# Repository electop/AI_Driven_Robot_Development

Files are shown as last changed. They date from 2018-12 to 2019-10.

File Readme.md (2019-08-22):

# Robot artist on the Champs Elysees
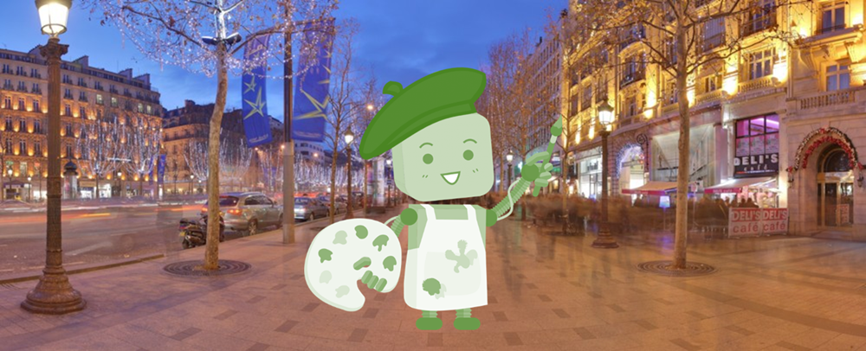
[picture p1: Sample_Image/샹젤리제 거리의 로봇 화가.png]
<br>

# Candidates for AI Driven Robot Development
1. Drawing Robot - Arduino Uno + CNC Shield + GRBL (May 27, 2017)<br>
https://www.thingiverse.com/thing:2349232<br>
https://www.youtube.com/watch?time_continue=3&v=vTD7USqdXJI<br>
Drawing Robot - Arduino Uno + CNC Shield + GRBL<br>
2. EEZYxyDRAW (Aug 24, 2018)<br>
https://www.thingiverse.com/thing:2936872<br>
EEZYxyDRAW<br>
3. drawbot (Sep 12, 2018)<br>
https://www.thingiverse.com/thing:3096135<br>
drawbot<br>
4. Cosmos Drawbot 1.0 (May 12, 2019)<br>
https://www.thingiverse.com/thing:3624736<br>
Cosmos Drawbot 1.0<br>
5. midTbot (Oct 16, 2017)<br>
https://www.thingiverse.com/thing:2587684<br>
http://www.buildlog.net/blog/2017/10/the-midtbot-a-new-flavor-of-h-bot/<br>
midTbot<br>
    - PCB DipTrace file : <a href="http://www.buildlog.net/blog/wp-content/uploads/2017/10/MidTBot_PCB_V1.zip">MidTBot_PCB_V1</a><br>
    - PCB Gerber file : <a href="http://www.buildlog.net/blog/wp-content/uploads/2017/10/midTbot_Gerber_v1.zip">midTbot_Gerber_v1</a>

# Summary for Drawing Robot
   - Configuration
        ```
        $0=10 (step pulse, usec)
        $1=25 (step idle delay, msec)
        $2=0 (step port invert mask:00000000)
        $3=0 (dir port invert mask:00000000)
        $4=0 (step enable invert, bool)
        $5=0 (limit pins invert, bool)
        $6=0 (probe pin invert, bool)
        $10=3 (status report mask:00000011)
        $11=0.010 (junction deviation, mm)
        $12=0.002 (arc tolerance, mm)
        $13=0 (report inches, bool)
        $20=0 (soft limits, bool)
        $21=0 (hard limits, bool)
        $22=0 (homing cycle, bool)
        $23=0 (homing dir invert mask:00000000)
        $24=25.000 (homing feed, mm/min)
        $25=500.000 (homing seek, mm/min)
        $26=250 (homing debounce, msec)
        $27=1.000 (homing pull-off, mm)
        $100=100.000 (x, step/mm) > GT2 Pully : 내경 5mm, 외경 13mm, 높이 14mm, Pitch 2mm, 16 teeth
        $101=100.000 (y, step/mm)
        $102=100.000 (z, step/mm)
        $110=3000.000 (x max rate, mm/min)
        $111=3000.000 (y max rate, mm/min)
        $112=3000.000 (z max rate, mm/min)
        $120=1000.000 (x accel, mm/sec^2)
        $121=1000.000 (y accel, mm/sec^2)
        $122=1000.000 (z accel, mm/sec^2)
        $130=300.000 (x max travel, mm)
        $131=220.000 (y max travel, mm)
        $132=200.000 (z max travel, mm)
        ```
   - Contents<br>
      This drawing robot is similar to the commercially available AxiDraw. It is powered by an Arduino Uno controller, uses a CNC Shield, and GRBL firmware. The approximate cost to build this drawing robot is $100.

      Assembly documentation can be found in the Files section and at the following link. Thanks to Jonathan K for supplying this documentation.<br>
      https://docs.google.com/presentation/d/1GihJuR7yHVtUPYCp9GVDHLsJUhT2RwPrkIopzYrXYhw/edit?usp=sharing

      There's also a document which explains how to install Inkscape, the Inkscape MI extension, and the Universal G-Code Sender. It guides you through three example projects and can be found in the Files section of this Thing. Use these instructions instead of the last three pages of the assembly document which describe a different G-Code extension.

      This drawing robot allows you to draw things in Inkscape and then plot them out. The drawing robot receives G Code commands that are created inside an Inkscape extension called MI. Below are the links to the software used. There's a document in the Files section explaining how to use the software.

      Print all the parts. Assemble them using the assembly guide and then use the installation and use guide to start using your Draw Robot.

      When setting up your hardware you must do the following:

      1. Be sure to install 3 jumpers on the CNC Shield for each stepper driver. There's a photo showing the jumpers.
      2. You must use the GRBL version pointed to in the link below. Replace the "config.h" file with the one provided which has the correct features enabled before you compile and download from the Arduino IDE. IF YOU FAIL TO PERFORM THIS STEP, the robot will draw at a 45 degree angle. Don't send me a message about this because it means you failed to perform this step
      3. Set the GRBL parameters to the settings that are provided in one of the photos. This step is missing from the otherwise excellent instructions. You must do this or the robot will not work.
      4. Be sure to set the correct MI Extension parameters the first time you get the MI extension pop up.
      5. If you have problems with your stepper motors moving and you believe everything else above is OK, check that the small current adjustment on your stepper drivers are set mid point and also set the drive current to 1 amp using the correct procedure for your driver.

      I have posted all the parts needed from the two source designs. There are only 15 parts to print and none of them are very large. I added a stronger pen slider and a controller enclosure. There is an even better pen holder in the remix section. I also clarified the names that were in Spanish. I have posted all needed files so that there isn't confusion regarding which parts are needed from each of the original designs.

      My drawing robot is modified version of this one<br>
      https://www.thingiverse.com/thing:2058866

      Place this version of GRBL Firmware for the Arduino on your computer. You must use this version of GRBL. Other GRBL versions do not have the control code for the Z axis servo.<br>
      https://github.com/robottini/grbl-servo

      Replace the default config.h file in GRBL with the one supplied in the "Thing Files" section

      Upload GRBL to your Arduino Uno using these instructions<br>
      https://github.com/grbl/grbl/wiki/Compiling-Grbl (Ignore references to GRBL V1.1)<br>
      You must copy the config.h which I supply here to the directory where GRBL resides and then do the upload. The new config.h will be used for the compile of the GRBL code.

      Inkscape Drawing Software<br>
      https://inkscape.org/en/

      Universal G-Code Sender<br>
      https://winder.github.io/ugs_website/download/<br>

      Use the Inkscape MI Extension to generate G Code:<br>
      http://www.mediafire.com/file/ae0wquqornzc3o2/MI+Inkscape+Extension.zip<br>
      There is a tutorial in the Files section on how to use the software.

## HARDWARE NEEDED<br>
2x Nema 17 Stepper Motors<br>
2x Linear bearing rod M8 x 450mm, X Axis<br>
2x Linear bearing rod M8 x 350mm, Y axis<br>
2x Linear rod M3 x 75mm, Z Axis<br>
(You can find them in any old CDROM or purchase on EBay)<br>
1x M8x470mm threaded rod<br>
8x LM8UU linear bearings or printed bearings<br>
1x sg90 Servo<br>
2x GT2 Pulley 16 teeth<br>
5x Bearing 624zz<br>
1x 2000mm GT2 belt

misc M3 and M4 screws and nuts<br>
M8 nuts

## ELECTRONICS<br>
Arduino Uno<br>
CNC Shield<br>
12V 2A Wall Transformer<br>
https://www.amazon.com/Adapter-100-240V-Transformers-Switching-Adaptor/dp/B019Q3U72M<br>
2-4 limit switches ( optional. I suggest you leave them off and add later if you want them)

## SOFTWARE<br>
Inkscape which is the graphics design software (draw or import graphics)<br>
Inkscape MI GRBL Extension (convert graphics to G-Code)<br>
Universal G Code Sender (sends the G-Code to the robot causing drawing motion)<br>
GRBL which is the Arduino firmware (programmed into the Arduino Uno)

I have supplied a few G Code files that work with this drawing robot. If your drawing robot is built identical to this design, the G Code files will also work with yours.

Here are a couple of videos of this drawing robot in action:<br>
https://youtu.be/vTD7USqdXJI<br>
https://youtu.be/kpTIFBDcTaY

Update 6-15-2017: I added the limit switches about 10 days ago and they don't add much to the functionality. When GRBL sees a limit switch hit, it just stops with an alarm condition. You must soft reset the robot and your drawing cannot be continued. The homing feature doesn't seem to work. I read in another persons post that they could not get home to work in GRBL 0.9. At this point I suggest building the drawing robot without the limit switches. As long as your drawing does not exceed the envelope of the robot, you won't need the limit switches.

Update 6-19-2017: My friend found a better Inkscape Extension for generating G Code.<br>
I think the MI Extension is easier to use and generates better G Code:<br>
http://www.mediafire.com/file/ae0wquqornzc3o2/MI+Inkscape+Extension.zip

Update 6-26-2017:<br>
I added the config.h file needed for GRBL for this machine. With this file and the GRBL parameter settings in the screen shot, you should be able to easily get your machine up and running. Don't forget to install the stepper driver jumpers.

Update 7-4-2017:<br>
The top and bottom clam shells did not fit without pushing the LM8UU bearings slightly out of alignment. I removed a small amount of material from the top clamshell to allow clearance for the bottom clamshell posts. The old Top_XY_clamshell.stl file has been removed and replaced with the Top_XY_clamshell_V4.stl file. Thanks to rocketmannate who caught this problem.

Update 11-18-2017<br>
Jonathan K. provided assembly documentation. Thanks you so much. I appreciate your efforts. Checkout the great PDF with excellent photos.

Update 3-11-2018<br>
I have had some questions from people whose drawing robots didn't work. Here are some things to check If your robot doesn't work:
Here are some things to check If your robot doesn't work:
Make sure you have the correct version of GRBL (the one pointed to in the description)
Make sure you copied the config.h file to your GRBL directory
Check your CNC jumpers. All three should be installed
Check that you entered the GRBL parameters using Universal G-Code sender
If your Z axis motor isn't working, make sure you have the correct version of GRBL and that you wired your servo to the correct pins.
Make sure you used the MI extension parameters shown in screenshot specifically M3 and M5 for up and down on Z servo

Update: Sept. 18, 2018<br>
If you have problems with your stepper motors moving and you believe everything else above is OK, check that the small current adjustment on your driver is set mid point and then set the drive current to 1 amp using the correct procedure for your driver.
Thanks to Ashkangh for catching this possible issue.

Update: January 4, 2019<br>
A few people have run into software errors when using the GRBL MI Extension. This extension depends on a software package called Python. Your computer may not have this package or it may have one that is older or newer than the one this robot was tested with. I suggest that you do a Google search if you get a xxxx.py" error and follow the instructions for correcting code or installation of Python.

Also:<br>
There are various Stepper Motor drivers that are slightly different. in some cases the current adjust pot is on the opposite end of the module which can be confusing when trying to plug it in based on my photos. Be sure to check the pin names and plug your module in with the pin names that match. I'm sorry but I don't have time to figure out your individual hardware configuration problems. This design works but it can require some troubleshooting if software or hardware is different than what I happened to use. When you figure out your problem, be sure to post the solution in the comments so that others may benefit from your experience.

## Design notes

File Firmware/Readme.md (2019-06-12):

### How to export hex file from arduino uno, using IDE
   - cmd
   - cd C:\Program Files (x86)\Arduino\hardware\tools\avr\bin
   - if com port is com7, execute "avrdude.exe -p m328p  -c arduino -C "..\etc\avrdude.conf" -P com7 -U flash:r:"C:\flash.hex":i" on "명령 프롬프트"
   ```
   C:\Program Files (x86)\Arduino\hardware\tools\avr\bin>avrdude.exe -p m328p  -c arduino -C "..\etc\avrdude.conf" -P com7 -U flash:r:"C:\flash.hex":i

   avrdude.exe: AVR device initialized and ready to accept instructions

   Reading | ################################################## | 100% 0.00s

   avrdude.exe: Device signature = 0x1e950f (probably m328p)
   avrdude.exe: reading flash memory:

   Reading | ################################################## | 100% 4.10s

   avrdude.exe: writing output file "C:\flash.hex"

   avrdude.exe: safemode: Fuses OK (E:00, H:00, L:00)

   avrdude.exe done.  Thank you.
   ```

### How to flash hex file into arduino uno, using IDE
   - cmd
   - cd C:\Program Files (x86)\Arduino\hardware\tools\avr\bin
   - if com port is com7 and there is hex file at C drive root, execute "avrdude.exe -p m328p  -c arduino -C "..\etc\avrdude.conf" -P com7 -U flash:w:"C:\flash.hex":i" on "명령 프롬프트"<br>
     if there is no available hex file, please use 'falsh.hex' on this path.
   ```
   C:\Program Files (x86)\Arduino\hardware\tools\avr\bin>avrdude.exe -p m328p  -c arduino -C "..\etc\avrdude.conf" -P com7 -U flash:w:"C:\flash.hex":i

   avrdude.exe: AVR device initialized and ready to accept instructions

   Reading | ################################################## | 100% 0.00s

   avrdude.exe: Device signature = 0x1e950f (probably m328p)
   avrdude.exe: NOTE: "flash" memory has been specified, an erase cycle will be performed
                To disable this feature, specify the -D option.
   avrdude.exe: erasing chip
   avrdude.exe: reading input file "C:\flash.hex"
   avrdude.exe: writing flash (32768 bytes):

   Writing | ################################################## | 100% 5.39s

   avrdude.exe: 32768 bytes of flash written
   avrdude.exe: verifying flash memory against C:\flash.hex:
   avrdude.exe: load data flash data from input file C:\flash.hex:
   avrdude.exe: input file C:\flash.hex contains 32768 bytes
   avrdude.exe: reading on-chip flash data:

   Reading | ################################################## | 100% 4.13s

   avrdude.exe: verifying ...
   avrdude.exe: 32768 bytes of flash verified

   avrdude.exe: safemode: Fuses OK (E:00, H:00, L:00)

   avrdude.exe done.  Thank you.
   ```

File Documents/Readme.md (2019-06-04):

# CR-10S & 10S4 & 10S5 사용정보(20190522)

## CR-10S & 10S4 & 10S5
출력방식 : FDM(Fused DEposition Modeling)<br>
출력사이즈 : 300*300*400 / 400*400*400 / 500*500*500<br>
프린터크기 : 525*270*635 / 610*290*740 / 730*285*840<br>
프린팅속도 : Normal 80mm/s, Max 200mm/s<br>
필라멘트 사이즈 : 1.75mm<br>
레이어두께 : 0.1~0.4mm (권장)<br>
노즐직경 : 0.4mm (0.2~1mm 사용가능, 0.4mm 사용추천)<br>
정밀도 : +(-)0.1mm<br>
익스트루더 : MK8 방식<br>
지원파일포맷 : STL, OBJ, G-Code<br>
입력방식 : USB(OnLine), SD Card(OffLine)<br>
무게 : 10.3kg / 11.5kg / 15.6kg<br>
기타사항 :<br>
- CR-10과 차이점 : Z축스텝모터가 더블, 필라멘트 감지센서<br>
- 정전시 이어서 출력가능<br>
- CR-10 시리즈와 엔더3는 레이저 각인기 운용이 가능합니다. https://cafe.naver.com/ddyair/999<br>

## 제품 판매링크
10S : http://dyairkorea.com/product/detail.html?product_no=12&cate_no=47&display_group=1<br>
10S4 : http://dyairkorea.com/prouct/detail.html?product_no=86&cate_no=47&display_group=1<br>
10S5 : http://dyairkorea.com/product/detail.html?product_no=25&cate_no=47&display_group=1<br>

**스페어파트**<br>
프로파일롤러 http://dyairkorea.com/product/detail.html?product_no=59&cate_no=31&display_group=1<br>
팬세트 http://dyairkorea.com/product/detail.html?product_no=56&cate_no=31&display_group=1<br>
스텝모터 http://dyairkorea.com/product/detail.html?product_no=51&cate_no=31&display_group=1<br>
http://dyairkorea.com/product/detail.html?product_no=50&cate_no=31&display_group=1<br>
커플러 http://dyairkorea.com/product/detail.html?product_no=47&cate_no=31&display_group=1<br>
빌드서페이스 http://dyairkorea.com/product/detail.html?product_no=58&cate_no=31&display_group=1<br>
파워서플라이 http://dyairkorea.com/product/detail.html?product_no=49&cate_no=31&display_group=1<br>
메인보드 http://dyairkorea.com/product/detail.html?product_no=48&cate_no=31&display_group=1<br>
히팅베드 http://dyairkorea.com/product/detail.html?product_no=53&cate_no=31&display_group=1<br>
LCD디스플레이 http://dyairkorea.com/product/detail.html?product_no=52&cate_no=31&display_group=1<br>
MK8 익스트루더 http://dyairkorea.com/product/detail.html?product_no=64&cate_no=31&display_group=1<br>
Z축지지대 http://dyairkorea.com/product/detail.html?product_no=61&cate_no=31&display_group=1<br>

## 기본적으로 알아야 할 내용

- 조립 : https://cafe.naver.com/ddyair/82<br>
- 베드레벨링 : https://cafe.naver.com/ddyair/85<br>
- 큐라설치 및 세팅 : 10S https://cafe.naver.com/ddyair/4865<br>
  10S5 https://cafe.naver.com/ddyair/4866<br>
- 노즐교체 영상(CR시리즈과 동일) : https://www.youtube.com/watch?v=Yhu3SahbN44<br>
- 4010팬 교체 동영상입니다.(팬 전압은 12V) : https://www.youtube.com/watch?v=Xu0QXxP7dHU&list=PL5UfhdgCEfhNQBHFDc15D-m7l7TStda3M&index=7&t=0s<br>
  구입처 : https://smartstore.naver.com/ssack3dprinterstore_dyair/products/3046827558<br>
- 노즐세트 교체 방법 : https://www.youtube.com/watch?v=AcJJXZxm2D4&list=PL5UfhdgCEfhNQBHFDc15D-m7l7TStda3M&index=9&t=0s<br>
- 구입처 : https://smartstore.naver.com/ssack3dprinterstore_dyair/products/3045667993<br>
- 조립 후 점검사항 : https://cafe.naver.com/ddyair/84<br>
- 콘트롤박스 메뉴 설명 : https://cafe.naver.com/ddyair/91<br>
- 테스트 리트렉션 : https://cafe.naver.com/ddyair/172<br>
- 출력온도 : https://cafe.naver.com/ddyair/157<br>
- 매쉬레벨링 업데이트 방법 : https://cafe.naver.com/ddyair/1265<br>
  2.0.0 베타버전 : https://cafe.naver.com/ddyair/3384<br>
- 출력물품질 높이는 히트브레이크(모델링 공유 사이트에서 다양한 형태를 선택할수 있습니다.)<br>
  https://cafe.naver.com/ddyair/1410<br>
- 오토레벨링 (Creality3D 센서) : https://cafe.naver.com/ddyair/1538<br>
- BL터치 설치 : https://cafe.naver.com/ddyair/2705<br>
  https://cafe.naver.com/ddyair/2735

## 제품관련 정보

- 출력 품질문제중 가장 많은 포인트, 익스트루더 업그레이드 추천 : https://cafe.naver.com/ddyair/3384<br>
구입처 : https://smartstore.naver.com/ssack3dprinterstore_dyair/products/3707329970<br>
프로파일 T너트 규격 검색 => 2020 T너트<br>
작동시 소모전력 테스트 : https://cafe.naver.com/ddyair/1159

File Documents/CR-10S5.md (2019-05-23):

# CR-10S & 10S4 & 10S5 사용정보(20190522)

## CR-10S & 10S4 & 10S5

출력방식 : FDM(Fused DEposition Modeling)

출력사이즈 : 300*300*400 / 400*400*400 / 500*500*500

프린터크기 : 525*270*635 / 610*290*740 / 730*285*840

프린팅속도 : Normal 80mm/s, Max 200mm/s

필라멘트 사이즈 : 1.75mm

레이어두께 : 0.1~0.4mm (권장) 

노즐직경 : 0.4mm (0.2~1mm 사용가능, 0.4mm 사용추천)

정밀도 : +(-)0.1mm

익스트루더 : MK8 방식

지원파일포맷 : STL, OBJ, G-Code

입력방식 : USB(OnLine), SD Card(OffLine)

무게 : 10.3kg / 11.5kg / 15.6kg

기타사항 :

- CR-10과 차이점 : Z축스텝모터가 더블, 필라멘트 감지센서

- 정전시 이어서 출력가능

- CR-10 시리즈와 엔더3는 레이저 각인기 운용이 가능합니다. https://cafe.naver.com/ddyair/999

## 제품 판매링크
10S : http://dyairkorea.com/product/detail.html?product_no=12&cate_no=47&display_group=1
10S4 : http://dyairkorea.com/prouct/detail.html?product_no=86&cate_no=47&display_group=1
10S5 : http://dyairkorea.com/product/detail.html?product_no=25&cate_no=47&display_group=1

스페어파트
프로파일롤러 http://dyairkorea.com/product/detail.html?product_no=59&cate_no=31&display_group=1
팬세트 http://dyairkorea.com/product/detail.html?product_no=56&cate_no=31&display_group=1
스텝모터 http://dyairkorea.com/product/detail.html?product_no=51&cate_no=31&display_group=1
http://dyairkorea.com/product/detail.html?product_no=50&cate_no=31&display_group=1
커플러 http://dyairkorea.com/product/detail.html?product_no=47&cate_no=31&display_group=1
빌드서페이스 http://dyairkorea.com/product/detail.html?product_no=58&cate_no=31&display_group=1
파워서플라이 http://dyairkorea.com/product/detail.html?product_no=49&cate_no=31&display_group=1
메인보드 http://dyairkorea.com/product/detail.html?product_no=48&cate_no=31&display_group=1
히팅베드 http://dyairkorea.com/product/detail.html?product_no=53&cate_no=31&display_group=1
LCD디스플레이 http://dyairkorea.com/product/detail.html?product_no=52&cate_no=31&display_group=1
MK8 익스트루더 http://dyairkorea.com/product/detail.html?product_no=64&cate_no=31&display_group=1
Z축지지대 http://dyairkorea.com/product/detail.html?product_no=61&cate_no=31&display_group=1

## 기본적으로 알아야 할 내용

- 조립
https://cafe.naver.com/ddyair/82

- 베드레벨링
https://cafe.naver.com/ddyair/85
- 큐라설치 및 세팅
10S https://cafe.naver.com/ddyair/4865
10S5 https://cafe.naver.com/ddyair/4866                                    

- 노즐교체 영상(CR시리즈과 동일)
https://www.youtube.com/watch?v=Yhu3SahbN44

- 4010팬 교체 동영상입니다.(팬 전압은 12V)
https://www.youtube.com/watch?v=Xu0QXxP7dHU&list=PL5UfhdgCEfhNQBHFDc15D-m7l7TStda3M&index=7&t=0s
구입처 https://smartstore.naver.com/ssack3dprinterstore_dyair/products/3046827558

- 노즐세트 교체 방법
 https://www.youtube.com/watch?v=AcJJXZxm2D4&list=PL5UfhdgCEfhNQBHFDc15D-m7l7TStda3M&index=9&t=0s

구입처 https://smartstore.naver.com/ssack3dprinterstore_dyair/products/3045667993

- 조립 후 점검사항
https://cafe.naver.com/ddyair/84                                    

- 콘트롤박스 메뉴 설명
https://cafe.naver.com/ddyair/91

- 테스트
리트렉션 https://cafe.naver.com/ddyair/172   출력온도 https://cafe.naver.com/ddyair/157     

- 매쉬레벨링 업데이트 방법
https://cafe.naver.com/ddyair/1265  2.0.0 베타버전 https://cafe.naver.com/ddyair/3384

- 출력물품질 높이는 히트브레이크(모델링 공유 사이트에서 다양한 형태를 선택할수 있습니다.)  
https://cafe.naver.com/ddyair/1410 

- 오토레벨링 (Creality3D 센서)
https://cafe.naver.com/ddyair/1538

- BL터치 설치
https://cafe.naver.com/ddyair/2705           https://cafe.naver.com/ddyair/2735

## 제품관련 정보

- 출력 품질문제중 가장 많은 포인트, 익스트루더 업그레이드 추천
https://cafe.naver.com/ddyair/3384  
구입처 https://smartstore.naver.com/ssack3dprinterstore_dyair/products/3707329970
프로파일 T너트 규격 검색 => 2020 T너트
작동시 소모전력 테스트 https://cafe.naver.com/ddyair/1159

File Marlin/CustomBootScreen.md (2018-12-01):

Article: http://community.robo3d.com/index.php?threads/custom-boot-screen-for-marlin-and-full-graphics-lcd.17221/
paint.net (image to bmp): https://www.dotpdn.com/files/paint.net.4.1.4.install.zip

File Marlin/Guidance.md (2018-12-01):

https://www.printedsolid.com/blogs/news/installing-marlin-1-1-6-on-your-cr-10s-with-mesh-bed-leveling

<div class="ten columns alpha blog_content">
      <p><strong>Important note about customer support of CR-10S Marlin update blog posts<span>.  These posts were written by David Randolph as a free community contribution.  He's happy to have provided this contribution when Creality would not.  Unfortunately, we do not have unlimited time and cannot provide support if you have any issues with this process.  Please read the instructions carefully and consider your skill level.  If you run into any issues, we suggest posting comments on this blog post as many users </span><span>hang out regularly and will offer help.  Checking into the various Facebook CR-10 Communities is also an option.  </span></strong></p>

<p><strong>UPDATE! </strong>We have added notes for the new version of Marlin 1.1.7 as well as a new download of the source and hex files. Enjoy</p>

<p>Before we start: This is for the <a href="https://printedsolid.com/products/cr10s">CR-10S</a> and not the CR-10. Don’t use this firmware or follow these instructions for the CR-10. It is a different board and uses different settings.The older CR-10 uses a MELZI board which has less memory so in order to get it to work you will have to remove a lot of options to get everything to fit.</p>
<p>The firmware for the CR-10S is based on Marlin <a href="http://marlinfw.org">http://marlinfw.org</a> which is an open source project and as such means you can modify the source code as you want. While this article will be long and involved, I will get right to the point and just give you the .hex file and you can go ahead and just install it and close out this page. This version has mesh bed leveling, baby stepping and EEPROM storage enabled.</p>
<p>Inside the zip is a file called instructions.pdf on how to flash your firmware.</p>
<p> <a href="https://cdn.shopify.com/s/files/1/0887/0138/files/CR-10S-Marlin_By_PrintedSolid.zip?18225442472906648344">CR-10S 1.1.6 Firmware Source Code and Hex Files</a></p>
<p><a href="https://cdn.shopify.com/s/files/1/0887/0138/files/CR-10S-Marlin_By_PrintedSolid_117.zip?18225442472906648344"> CR-10S 1.1.7 Firmware Source Code and Hex Files</a></p>
<p>However, if you’re still reading this then we will go ahead and get moving. Let’s install and configure the software and give you a quick lesson on what we will be doing.</p>
<ol>
<li>You will need to download and install the Arduino IDE. <a href="https://www.arduino.cc/en/Main/Software">https://www.arduino.cc/en/Main/Software</a>
</li>
<li>Next you will need to download and install the U8glib library. <a href="https://bintray.com/olikraus/u8glib/download_file?file_path=u8glib_arduino_v1.18.1.zip">https://bintray.com/olikraus/u8glib/download_file?file_path=u8glib_arduino_v1.18.1.zip</a> and then from inside Arduino go to <em>sketch&gt;include library&gt;add zip library </em>and select the zip file. This is a library used to run the LCD display.</li>
<li>A preference we should setup inside of Arduino is to show line numbers. This will help us guide our way through the code and I will be referring to line numbers and the variable names for version 1.1.6. If you are reading this and using a different firmware version then line numbers may have changed but most likely the variable names will be the same. Now in the Arduino software go to <em>File&gt;Preferences</em> and put a check mark in the box next to Display Line Number.</li>
<li>Finally you need to download the 1.1.6 firmware <a href="http://marlinfw.org/meta/download/">http://marlinfw.org/meta/download/</a> and unzip the folder. Don’t rename the folder or move the files around inside it. You can put it anywhere you like to work on it. Go into the folders till you find Marlin.ino and open that file from inside Arduino IDE. It will open the full project and put all the files into separate tabs along the top.</li>
</ol>
<p>Now we are ready to get to work modifying things. Most of the work we will be doing will be in <em>Configuration.h </em>but we will be touching a few other ones. I will call those out later on. In Arduino if a line is “commented” this means that the instructions on that line are ignored. Marlin is well written and most of what we be doing is uncommenting an option or changing a value of something. To uncomment a line you just remove the two forward slashes // at the beginning of the line. To comment out a line you will just and // at the start of the line.</p>
<h1>Configurations.h</h1>
<p>Line 114: <strong>#define BAUDRATE 115200 </strong></p>
<p><em>This is the speed that it communicates over USB. It could be one of the faster speeds but honestly this is enough.</em></p>
<p>Line 122: <strong>#define MOTHERBOARD BOARD_RAMPS_14_EFB</strong></p>
<p><em>There are many boards that support Marlin and this is one of them. It is based off the very popular board RAMPS.</em></p>
<p>Line 127: <strong>#define CUSTOM_MACHINE_NAME "CR-10S"</strong></p>
<p><em>When your machine starts up this is the name that is displayed in the bottom left of the screen. It can be anything you want between the quotes, even Printer McPrintface if you like.</em></p>
<p>Line 286: (Line 289 in Marlin 1.1.7) <strong>#define TEMP_SENSOR_0 1</strong></p>
<p><em>This sets the type of sensor used for measuring the hotend temperature. For the stock hotend you will use “1” and for an E3Dv6 hotend you will use “5”  </em></p>
<p>Line 291:  (Line 294 in Marlin 1.1.7) <strong>#define TEMP_SENSOR_BED 5</strong></p>
<p><em>This sets the bed sensor for the stock bed.</em></p>
<p>Line 325: (Line 328 in Marlin 1.1.7) <strong>#define HEATER_0_MAXTEMP 250</strong></p>
<p><em>This is the limit for how hot your hotend will go. For the stock hotend you should set it for 250 and for an E3Dv6 hotend you can set it to 300.</em></p>
<p>Line 330: (Line 333 in Marlin 1.1.7) <strong>#define BED_MAXTEMP 120</strong></p>
<p><em>This is the limit for how hot your bed will go. In this case we can set it to 120 but honestly you will be lucky to ever go above 80c.</em></p>
<p>Line 442: (Line 446 in Marlin 1.1.7) <strong>#define THERMAL_PROTECTION_HOTENDS</strong></p>
<p>Line 443: (Line 447 in Marlin 1.1.7)<strong> #define THERMAL_PROTECTION_BED<br></strong></p>
<p><em>These two lines are what protects your machine from thermal runaway. While they are already uncommented I wanted to still point them out so you know to pay attention to them.</em></p>
<p>Line 528: (Line 532 in Marlin 1.1.7) <strong>#define DEFAULT_AXIS_STEPS_PER_UNIT   { 80, 80, 400, 95 }</strong></p>
<p><em>This is the amount of steps your printer has to use to move a specific distance. Things like drivers, motors, gearing, screws can change these numbers but the ones above are good for a stock CR-10S. These can be tuned later from the control screen thanks to the EEPROM settings we will be enabling later.</em></p>
<p>Line 535: (Line 539 in Marlin 1.1.7) <strong>#define DEFAULT_MAX_FEEDRATE          { 2500, 2500, 100, 25 }</strong></p>
<p><em>This is the fastest the machine will move in all directions. </em></p>
<p>Line 553:  (Line 557 in Marlin 1.1.7) <strong>#define DEFAULT_ACCELERATION          575</strong></p>
<p><em></em>Acceleration is the rate of change of speed.  It is defined in mm/s^2.  Your printer slows down when changing direction and then speeds back up again in straight lines.  This line is the acceleration the printer will make during printing moves.  575 is fairly slow, but for a printer like the CR10S with a big moving bed, it will help prevent <a href="https://printedsolid.com/blogs/news/a-solid-foundation-for-high-quality-corners">ringing</a>.  </p>
<p>Line 554: (Line 558 in Marlin 1.1.7) <strong>#define DEFAULT_RETRACT_ACCELERATION  1000</strong></p>
<p><em>This is the acceleration applied to your extruder retraction.  You want this as high as it can go before the filament starts stripping out to help prevent strining.</em></p>
<p>Line 555: (Line 559 in Marlin 1.1.7) <strong>#define DEFAULT_TRAVEL_ACCELERATION   1000</strong></p>
<p><em>This is the acceleration of your printer when it is not printing.  Since it is not printing at the time, it can be a little higher since you won't be able to see the ringing.  If it is too high, you could see skipped steps and layer shifts.</em></p>
<p>Line 745: (Line 751 in Marlin 1.1.7) <strong>#define INVERT_X_DIR false</strong></p>
<p>Line 746: (Line 752 in Marlin 1.1.7) <strong>#define INVERT_Y_DIR false</strong></p>
<p>Line 747: (Line 753 in Marlin 1.1.7) <strong>#define INVERT_Z_DIR true</strong></p>
<p><em>These 3 line define the direction of each axis. If your machine moves in the opposite direction of what you expect then change it to true or false.</em></p>
<p>Line 777: (Line 783 in Marlin 1.1.7) <strong>#define X_BED_SIZE 300</strong></p>
<p>Line 778: (Line 784 in Marlin 1.1.7) <strong>#define Y_BED_SIZE 300</strong></p>
<p>Line 786: (Line 792 in Marlin 1.1.7) <strong> #define Z_MAX_POS 400</strong></p>
<p><em>This is where we set the actual bed size of your printer and the Z height.</em></p>
<p>Line 801: (Line 827 in Marlin 1.1.7) Uncomment <strong>#define FILAMENT_RUNOUT_SENSOR</strong></p>
<p><em>This will enable the filament sensor. </em></p>
<p>Line 803: (Line 829 in Marlin 1.1.7) <strong>#define FIL_RUNOUT_INVERTING true</strong></p>
<p><em>Here we are changing the way the switch on the filament sensor works.</em></p>
<p>Line 855: (Line 876 in Marlin 1.1.7) Uncomment<strong> #define MESH_BED_LEVELING</strong></p>
<p><em>This is the fun part. No probe, no hardware. This allows you to level the bed at multiple points manually and it will create a 3D mesh of the surface to allow you to print on an uneven bed.  It will use the manual bed leveling as defined <a href="http://marlinfw.org/docs/features/unified_bed_leveling.html">here</a>. </em></p>
<p>Line 874:  (Line 986 in Marlin 1.1.7) <strong>#define GRID_MAX_POINTS_X 3</strong></p>
<p><em>We are setting this to 3 which means it will have you level 3 times along the X axis and 3 times along the Y axis for a total of 9 points. If you set this to 5 then it would mean you have to adjust level 25 times on the bed. 3 is a really good number for this.</em></p>
<p>Line 956: (Line 997 in Marlin 1.1.7) Uncomment<strong> #define LCD_BED_LEVELING<br></strong></p>
<p><em>This adds the option to run mesh bed leveling to the LCD screen.</em></p>
<p>Line 964:  (Line 1005 in Marlin 1.1.7) Uncomment<strong> #define LEVEL_BED_CORNERS<br></strong></p>
<p><em>This adds the option to level the corners of your bed before running mesh leveling.</em></p>
<p>Line 1018: (Line 1116 in Marlin 1.1.7) <strong> </strong>Uncomment<strong> #define EEPROM_SETTINGS</strong></p>
<p><em>This allows you to adjust things like offsets and steps and store them.</em></p>
<p>Line 1019: (Line 1117 in Marlin 1.1.7)<strong> </strong>Uncomment<strong> #define DISABLE_M503</strong></p>
<p><em>This is a command that shows the settings as they were set in the firmware and not the ones you changed in the EEPROM. We are disabling this to save some memory.</em></p>
<p>Line 1050 (Line 1148 in Marlin 1.1.7):<strong> #define PREHEAT_1_TEMP_HOTEND 205</strong></p>
<p>Line 1051 (Line 1149 in Marlin 1.1.7):<strong> #define PREHEAT_1_TEMP_BED     60</strong></p>
<p>Line 1052 (Line 1150 in Marlin 1.1.7):<strong> #define PREHEAT_1_FAN_SPEED     0</strong></p>
<p>Line 1054 (Line 1152 in Marlin 1.1.7):<strong> #define PREHEAT_2_TEMP_HOTEND 250</strong></p>
<p>Line 1055 (Line 1153 in Marlin 1.1.7):<strong> #define PREHEAT_2_TEMP_BED     80</strong></p>
<p>Line 1056 (Line 1154 in Marlin 1.1.7):<strong> #define PREHEAT_2_FAN_SPEED     0</strong></p>
<p><em>The lines 1050-1056 set the temps and fan speeds for the menu items to preheat for PLA and ABS.</em></p>
<p>Line 1232: (Line 1330 in Marlin 1.1.7): Uncomment <strong>#define SDSUPPORT</strong></p>
<p><em>This enables the SD card slot so you can print from SD.</em></p>
<p>Line 1257: (Line 1355 in Marlin 1.1.7): Uncomment <strong>#define ENCODER_PULSES_PER_STEP 1</strong></p>
<p><em>Leave this at 1 for the CR-10S</em></p>
<p>Line 1263 (Line 1361 in Marlin 1.1.7): Uncomment <strong>#define ENCODER_STEPS_PER_MENU_ITEM 5</strong></p>
<p><em>This is how far the knob needs to turn to move between menu items. Make this number lower if it is too sensitive and higher if it is not.</em></p>
<p>Line 1303: (Line 1401 in Marlin 1.1.7): Uncomment <strong>#define SPEAKER</strong></p>
<p><em>This will let the machine beep and make sounds.</em></p>
<p>Line 1384 (Line 1482 in Marlin 1.1.7): Uncomment <strong>#define REPRAP_DISCOUNT_FULL_GRAPHIC_SMART_CONTROLLER</strong></p>
<p><em>This enables the LCD screen. When we first installed U8Glib library, it was for this option.</em></p>
<p>Line 1684 (Line 140 in Marlin 1.1.7): #define <strong>DEFAULT_NOMINAL_FILAMENT_DIA 1.75 </strong> </p>
<p><em>Here we set what size filament will be used in the machine.</em></p>

<h1>Configuration_adv.h</h1>
<p>Line 602 (Line 658 in Marlin 1.1.7): Uncomment <strong>#define BABYSTEPPING</strong></p>
<p><em>Baby stepping allows you to adjust the Z axis while printing to help get the perfect 1<sup>st</sup> layer.</em></p>
<p>Line 606 (Line 662 in Marlin 1.1.7):  <strong>#define BABYSTEP_MULTIPLICATOR 5</strong></p>
<p><em>This is how much your Z axis will move per rotation on the knob. I find 5 is a good number but if you want finer control then lower this number. IF you want it to move more per click then increase this number.</em></p>
<p>Line 608 (Line 664 in Marlin 1.1.7): Uncomment <strong>#define DOUBLECLICK_FOR_Z_BABYSTEPPING</strong></p>
<p><em>This makes it so if you want to adjust baby stepping then you can press the control knob two times quickly and you will enter baby step mode.</em></p>
<p>Line 683 (Line 733 in Marlin 1.1.7): Comment out <strong>// #define ARC_SUPPORT</strong></p>
<p><em>Not really used since most slicers don’t do this function by default. If we disable it then we save even more memory.</em></p>
<p>Line 819 (Line 878 in Marlin 1.1.7): Uncomment <strong>#define ADVANCED_PAUSE_FEATURE</strong></p>
<p><em>This is for the filament runout sensor. It will home the hotend and unload the filament from the nozzle. Then once you load more filament it will wait till it’s extruding before beginning the print.</em></p>
<h1>Pins_RAMPS.h</h1>
<p>Line 206 (Line 255 in Marlin 1.1.7): <strong>#define FIL_RUNOUT_PIN      2</strong></p>
<p><em>We are changing this one value from 4 to 2 so we are using the right pin for the filament sensor.</em></p>
<p><em> </em></p>
<h2><strong>All done! Save your work.</strong></h2>
<p>Wow, you really have been sticking with me this whole time and you have modified everything and you are ready to build your firmware and install it. Kudos for sticking with me this whole time.</p>
<ol>
<li>
<em> </em>Select <em>Tools&gt;Board&gt;Arduino/Genuino Mega or Mega 2560</em> and then <em>Tools&gt;Processor&gt;ATMega2560 (Mega 2560) </em>and then select the COM port for your printer. Did I mention that you should have already plugged your printer into your computer?</li>
<li>
<em> </em>Now we want to verify and compile the code. You can do this by clicking on the checkmark icon in the tool bar or by going to <em>Sketch&gt;Verify/Compile </em>
</li>
<li>
<em> </em>If you got no errors then congratulations and now you are ready to upload the firmware. Go to Sketch&gt;Upload or click on the icon in the toolbar that is an arrow pointing to the right.</li>
<li>
<em> </em>Now you are all set and good to go, enjoy your new firmware. Let us know what you think and if you think we should do anything more.</li>
</ol>

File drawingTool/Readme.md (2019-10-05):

## DrawingTool
  ### History
    DrawigTool
    1. v0.001 : 2019-08-23 12:35 by Bongchae Kim
    2. v0.002 : 2019-08-25 11:45 by Bongchae Kim
    3. v0.003 : 2019-09-06 11:34 by Bongchae Kim
    4. v0.004 : 2019-09-09 19:09 by Bongchae Kim
    5. v0.005 : On going

  ### User scenarios
    1. User can import an image file. It's necessary to draw picture as a sketch.
    2. User can get G-codes with a sketch.
    3. User can define the thickness of the line. Of course, it will be also implemented to be able to draw with G-codes, considering the thickness.

  ### Figures
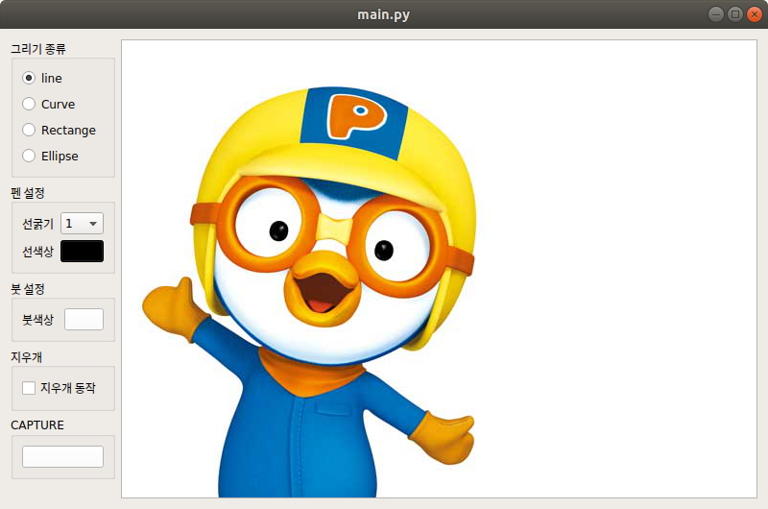
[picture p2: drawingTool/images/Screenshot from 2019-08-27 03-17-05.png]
<br>

## Cartoonizer
  ### History
    1. v0.001 : 2019-08-23 08:31 by Ju-hwan Yoo
    2. v0.002 : On going

  ### User scenarios
    1. User can get cartoon image from web cam device.

  ### Figures
  #### e.g.1
  ##### ▶ Source
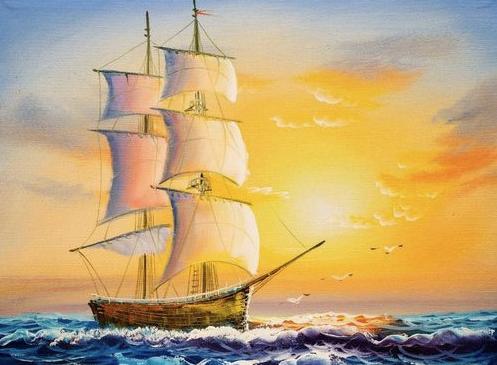
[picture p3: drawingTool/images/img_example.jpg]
  <br>
  ##### ▶ Edge mask
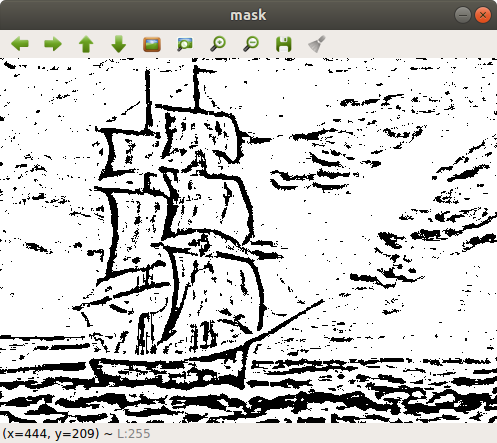
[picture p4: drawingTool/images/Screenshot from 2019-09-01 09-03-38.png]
  <br>
  ##### ▶ Gaussian pyramid + Edge mask
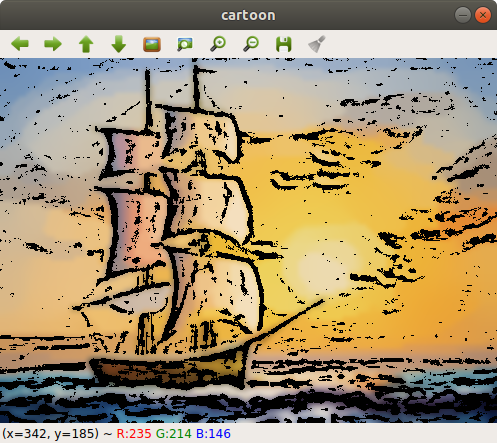
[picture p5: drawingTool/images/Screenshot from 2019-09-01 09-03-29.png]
  <br>
  #### e.g.2
  ##### ▶ Source
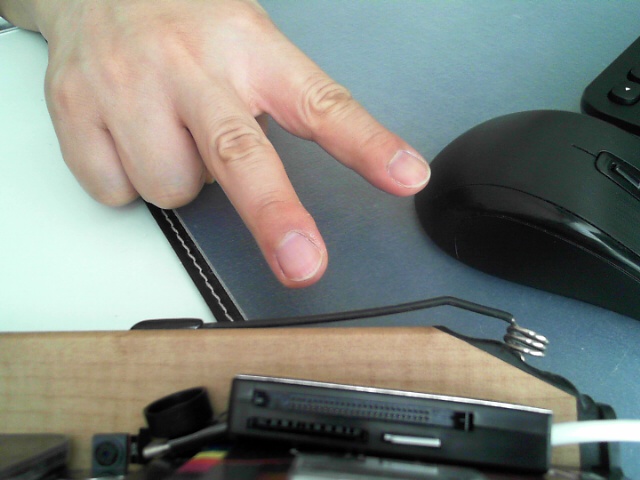
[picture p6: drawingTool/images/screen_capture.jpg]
  <br>
  ##### ▶ Edge mask
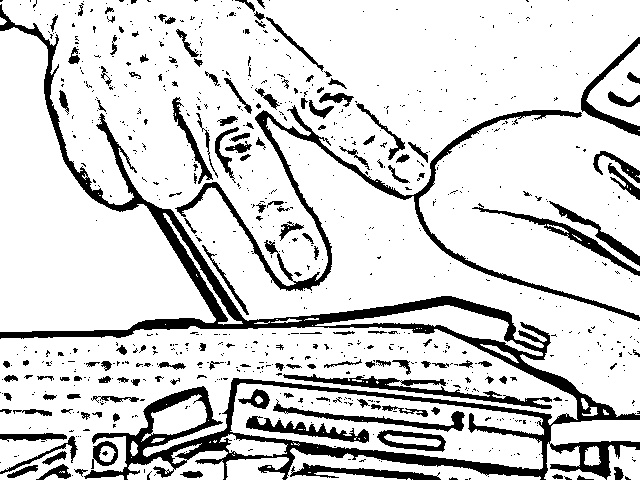
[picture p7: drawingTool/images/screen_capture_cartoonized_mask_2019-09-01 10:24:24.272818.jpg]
  <br>
  ##### ▶ Gaussian pyramid + Edge mask
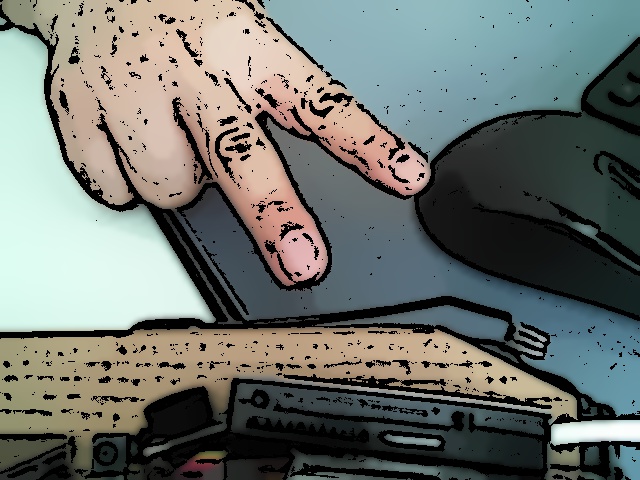
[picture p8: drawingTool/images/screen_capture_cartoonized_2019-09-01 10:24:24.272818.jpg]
  <br>
  #### e.g.3
  ##### ▶ Edge mask (vs) Edge mask + Median blur
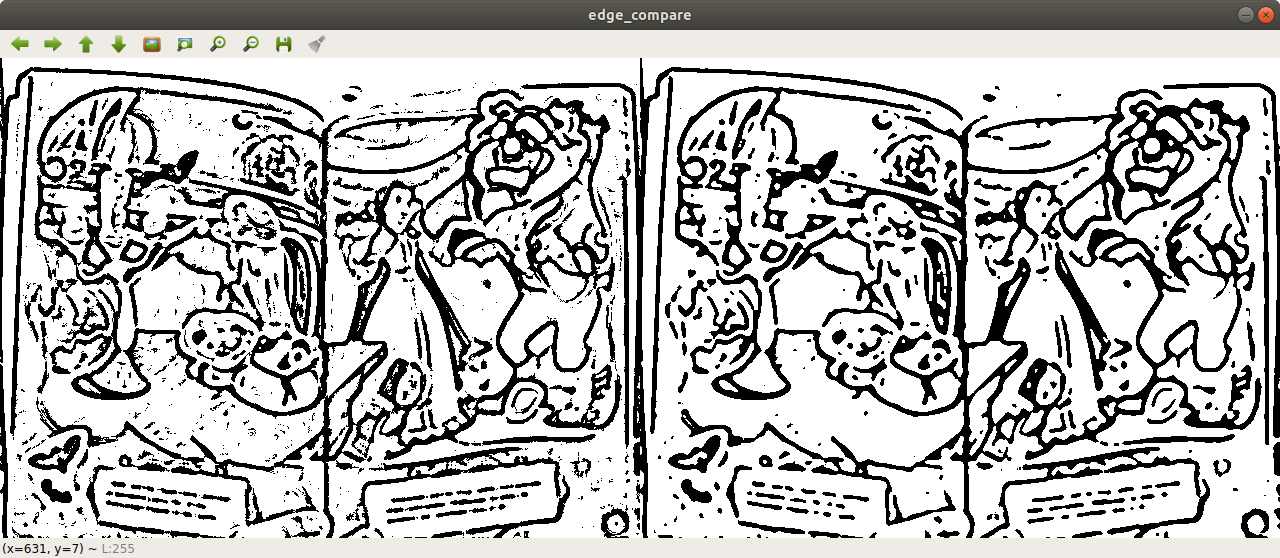
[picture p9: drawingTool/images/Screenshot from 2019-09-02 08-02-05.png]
  <br>
  ##### ▶ Source (vs) Gaussian pyramid + Edge mask + Median blur
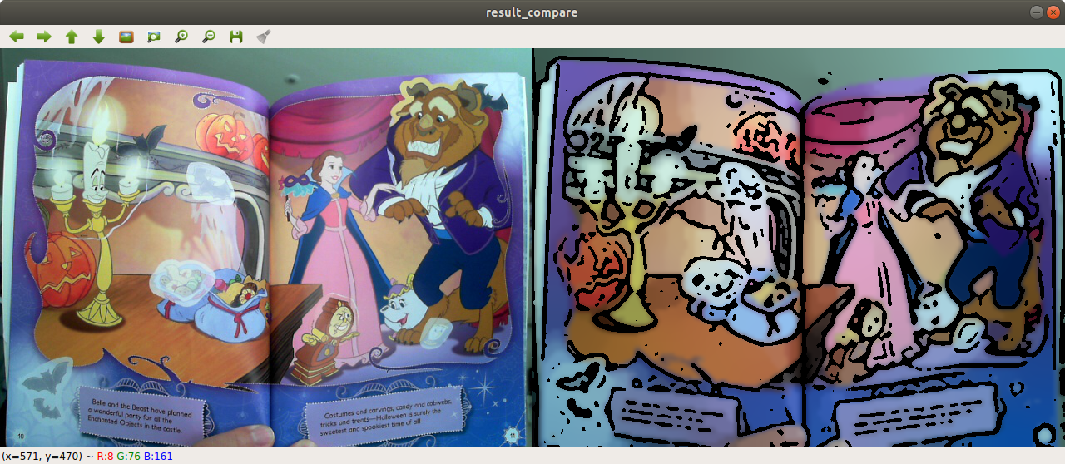
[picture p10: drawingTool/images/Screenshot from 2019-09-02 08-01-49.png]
  <br>

## Drawing Bot Desk design
  ### History
    1. V.0.001 : 2019-09-12 I added laser cutting design for desk.
    
  ### Figures
  #### Design Images
  ##### ▶ Top
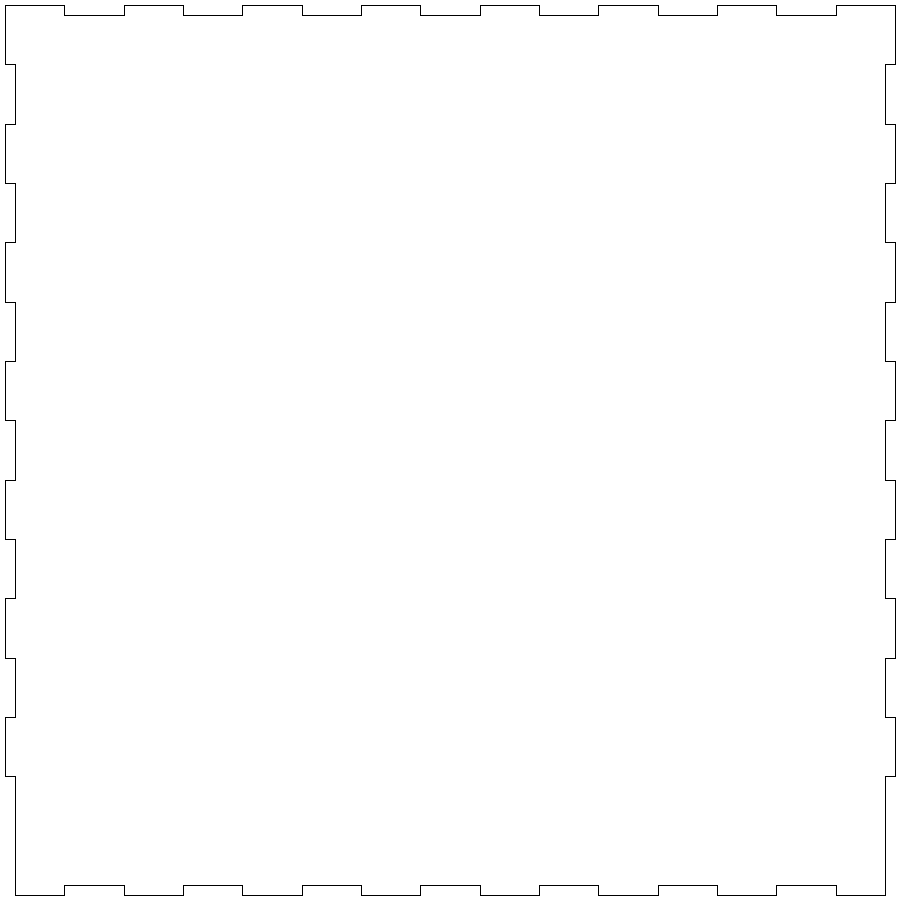
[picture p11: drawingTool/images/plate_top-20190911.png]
  <br>
  ##### ▶ Back
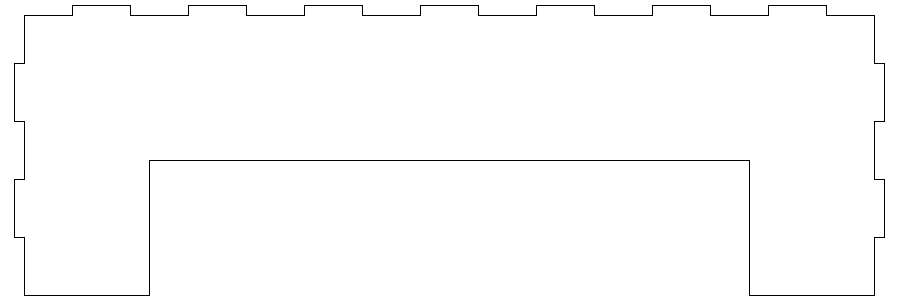
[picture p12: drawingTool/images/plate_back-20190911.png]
  <br>
  ##### ▶ Front
  <br>
  ##### ▶ Right
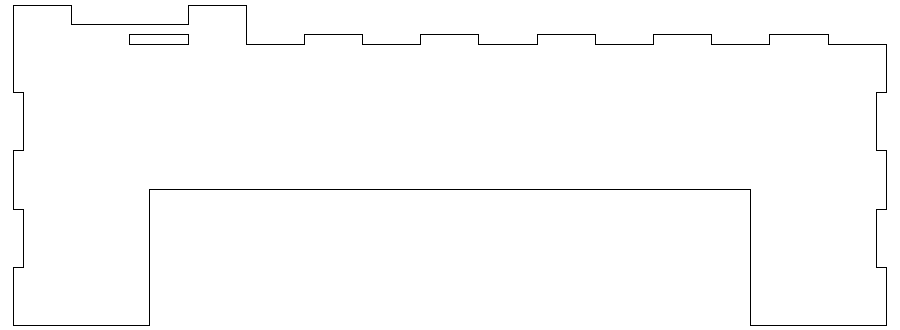
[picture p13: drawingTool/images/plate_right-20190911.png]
  <br>

## SW Update Requirement
  ### History
    1. V.0.002 : 2019-10-05 List for requirements
  #### 수정 필요 리스트
    1. Drawing Bot Serial Port 찾아서 붙이는 기능 (현재는 하드 코딩 되어 있음)
    2. Gcode 파일 별도 생성 필요 프로그램 오픈하면서 gcode 파일을 생성하게 되어 있고 여기에 바로 작성
    3. 당장은 바꾸지 않아도 되나 곡선을 그리면 펜이 내려온 상태에서 얻어지는 점 숫자가 너무 많아짐
       이를 근사화해서 곡선으로 (현재는 점에서 점으로 직선 형태) 변화하는 방법이 필요 (CAD 기술인데 잘 안찾아짐)
    4. 사진 찍었을 때 그림으로 만드는 파라메터 최적화
    5. 잘못그린 것 되돌리는 기능 (이건 복잡한게 지금 gcode에 바로 작성하게 되어 있어 이것도 돌려야 함)
    6. 기본 배경 gcode 확보 (간단하면서도 미적 감각이 있는 배경... 샹제리제 거리 또는 메이커 페어 관련)
    7. 혹시 웹캠을 쓸 경우 여러개의 카메라에서 웹캠을 찾아 선택하는 기

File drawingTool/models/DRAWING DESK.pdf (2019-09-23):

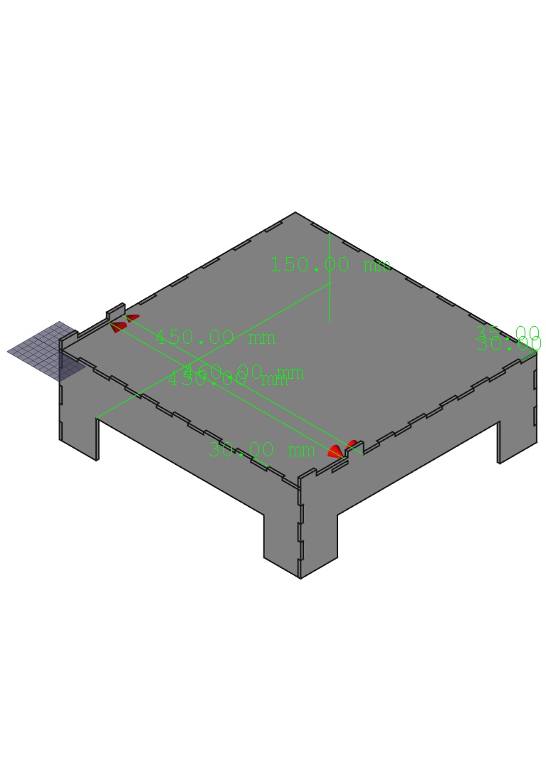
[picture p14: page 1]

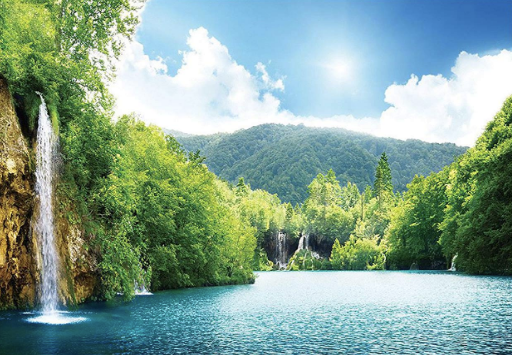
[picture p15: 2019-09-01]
drawingTool/images/img_example.png

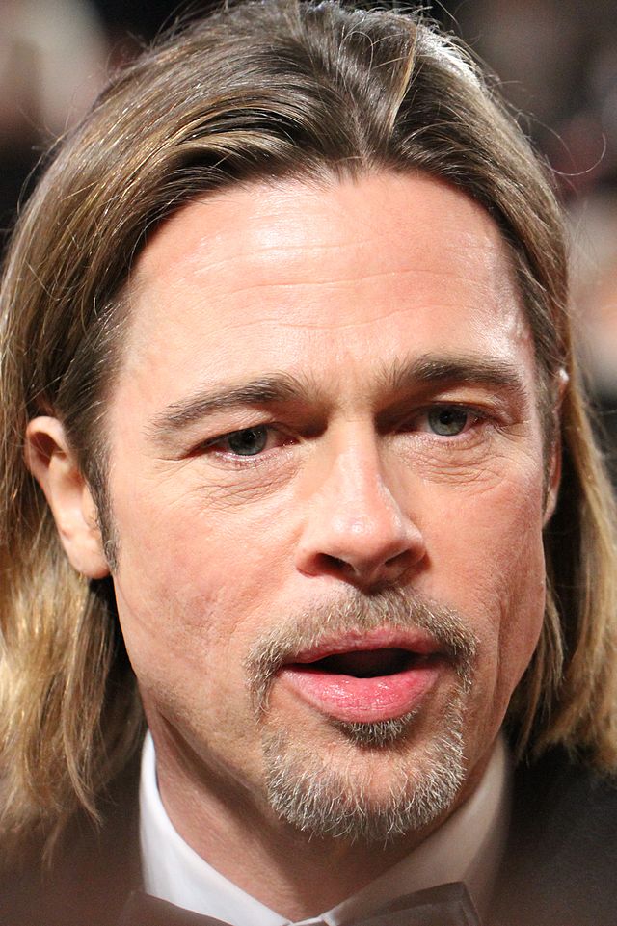
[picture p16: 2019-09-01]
drawingTool/images/640px-Brad_Pitt_2012.jpg

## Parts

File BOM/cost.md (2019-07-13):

### 지출 : 601,171
### 잔여예산 : -1,171

구입처|구매일| 비용 |내역
---	|	---	|	---	|	---
화성볼트|2019-07-13| 11,550 | M3 볼트/너트/와셔 등
창신상사|2019-07-13| 23,100 | 604 5개, 606 10개 베어링 구매
11번가|2019-07-10| 17,800 |DM741 스텝 모터 28BYj-48(드라이버포함)
지마켓|2019-06-09| 10,480 |CG0 서보모터 연장케이블
내써팝|2019-06-09| 15,300 |타이밍 풀리 6m, GT2 벨트 고정 클립, 피딩 스프링
AliExpress|2019-06-09| 38,424 |New Magnetic Print Bed 200mm Build Plate Tape Flex Palte Update 3D Printer
영원툴|2019-06-04| 4,540 |M8 너트, 와셔
AliExpress|2019-05-20| 5,189 |2pcs chrome steel Cylindrical roller Dowel Locating Pin M3 M4 M5 3mm / 4mm / 5mm * 50 55 60 70 80 mm Smooth Rods Linear Shaft
베어링가계|2019-05-20| 84,600 |열처리 연마봉 M8x350mm(6), M8x450mm(6)
내써팝|2019-05-17| 31,950 |타이밍 풀리 GT2 기어 1... 외 3개
Amazon|2019-01-2| 99,324 |304 Stainless Steel Screws Nuts and Washers 1200PCS, Sutemribor M2 M3 M4 Hex Socket Head Cap Bolts Screws Nuts Washers Assortment Kit with Three Hex Wrenches
서브무역|2018-12-30| 16,900 |실리콘 구리스 뿌리는 그리스 스프레이 (3M 실리콘 루브리컨트)
Amazon|2018-12-17| 51,934 |2 of LE Power Adapter, 2A, AC 100-240V to DC 12V Transformer, 24W Switching Power Supply, US Plug Power Converter for LED Strip Light and More, Pack of 2
미스터조각기|2018-12-17| 100,200 |ANET A8 NEMA17 ... 외 1개
삼디몰|2018-12-17| 14,500 |엔드스탑 스위치(가로형)-[리미트스위치]
손잡이닷컴|2018-12-17| 7,000 |전산볼트(절단서비스)
협신전자|2018-12-17| 6,640 |아두이노 SG-90 DXW90 서보모터 Arduino SG90 Servo Motor
영원툴|2018-12-17| 6,820 |와샤 와셔 평 스프링 M3 ... 외 11개
디에스엠알오|2018-11-22| 14,050 |[400-1724]두께게이지
신세계몰|2018-11-15| 20,400 |[신세계몰]브니엘 스쿼시볼 블루도트 옐로우도트 스쿼시공
옥션|2018-11-15| 20,470 |지아이엘 버니어 캘리퍼스 디지털 측정도구 노기스 켈리퍼스

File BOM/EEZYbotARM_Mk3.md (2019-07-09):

<br>

No.	|	Check	|	Category	|	Name	|	Num	|	Unit Price	|	 Price 	|	Description	|	Seller	|	Link fo shopping
---	|	---	|	---	|	---	|	---	|	---	|	---	|	---	|	---	|	---
1	|	O	|	H/W	|	DM741 스텝 모터 28BYj-48(드라이버포함)	|	3	|	 1,700 	|	 5,100 	|		|	11번가(비앤씨0)	|	http://www.11st.co.kr/product/SellerProductDetail.tmall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
2	|	O	|	H/W	|	아두이노 SG-90 DXW90 서보모터 Arduino SG90 Servo Motor	|	1	|	 1,370 	|	 1,370 	|		|	네이버쇼핑(협신전자)	|	https://smartstore.naver.com/ic11401/products/550103576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
3	|	O	|	H/W	|	Radial Bearing	606	|	2	|	 990 	|	 1,980 	|		|	네이버쇼핑(레셔널 마켓)	|	https://smartstore.naver.com/rationalmarket/products/2297125013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
4	|	O	|	H/W	|	Radial Bearing	604	|	1	|	 200 	|	 200 	|		|	네이버쇼핑(제페토닷컴)	|	https://smartstore.naver.com/xepetto/products/4357657315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

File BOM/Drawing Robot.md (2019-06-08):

No.	|	Check	|	Category	|	Name	|	Num	|	Unit Price	|	 Price 	|	Description	|	Seller	|	Link fo shopping
---	|	---	|	---	|	---	|	---	|	---	|	---	|	---	|	---	|	---
1	|	O	|	H/W	|	Nema 17 Stepper Motors	|	2	|	 7,700 	|	 15,400 	|		|	미스터조각기	|	https://smartstore.naver.com/mrcnc/products/2097373008
2	|	O	|	H/W	|	 Linear bearing rod M8 x 450mm	|	2	|	 7,650 	|	 15,300 	|	X Axis	|	베어링가게	|	https://smartstore.naver.com/allbearing/products/403940030
3	|	O	|	H/W	|	Linear bearing rod M8 x 350mm	|	2	|	 5,950 	|	 11,900 	|	Y axis	|	베어링가게	|	
4	|	O	|	H/W	|	Linear rod M3 x 75mm	|	2	|	865	|	1,730	|	Z Axis (You can find them in any old CDROM or purchase on EBay)	|	AliExpress	|	https://www.aliexpress.com/item/2pcs-chrome-steel-Cylindrical-roller-Dowel-Locating-Pin-M3-M4-M5-3mm-4mm-5mm-50-55/32889122344.html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,searchweb201602_5_10065_10068_319_10059_10884_317_10887_10696_321_322_10084_453_10083_454_10103_10618_10307_537_536,searchweb201603_52,ppcSwitch_0&algo_expid=73960c0a-ef12-4e23-8842-feef94211e86-3&algo_pvid=73960c0a-ef12-4e23-8842-feef94211e86&transAbTest=ae803_4
5	|	O	|	H/W	|	M8 x 470mm threaded rod	|	1	|	 4,500 	|	 4,500 	|		|	내써팝	|	https://smartstore.naver.com/nasspop/products/3559839665
6	|	O	|	H/W	|	LM8UU linear bearings or printed bearings	|	8	|	 600 	|	 4,800 	|		|	내써팝	|	https://smartstore.naver.com/nasspop/products/549934645
7	|	O	|	H/W	|	GT2 Pulley 16 teeth	|	2	|	 500 	|	 1,000 	|		|	내써팝	|	https://smartstore.naver.com/nasspop/products/337008823
8	|	O	|	H/W	|	Bearing 624zz	|	5	|	 250 	|	 1,250 	|		|	내써팝	|	https://smartstore.naver.com/nasspop/products/337005985
9	|	O	|	H/W	|	2000mm GT2 belt	|	1	|	 2,600 	|	 2,600 	|		|	내써팝	|	https://smartstore.naver.com/nasspop/products/337008935
10	|	O	|	H/W	|	sg90 Servo	|	1	|	 1,380 	|	 1,380 	|		|	협신전자	|	https://smartstore.naver.com/ic11401/products/550103576
11	|	O	|	H/W	|	Cap head M3 x 30mm screws and nuts	|	4	|	50+10	|	 240 	|		|	영원툴	|	https://smartstore.naver.com/0109/products/2185058720
12	|	O	|	H/W	|	Button/Philips head M4 x 15mm screws and nuts	|	4	|	40+10	|	 200 	|		|		|	
13	|	O	|	H/W	|	Button/Philips head M4 x 20mm screws and nuts	|	1	|	40+10	|	 50 	|		|		|	
14	|	O	|	H/W	|	Button/Philips head M3 x 10mm screws and nuts	|	8	|	30+10	|	 320 	|		|		|	
15	|	O	|	H/W	|	Cap head M3 x 15mm screws	|	1	|		|		|		|		|	
16	|	O	|	H/W	|	Flat head M3 x 15mm screws	|	3	|		|		|		|		|	
17	|	O	|	H/W	|	M8 nuts	|	50	|	30	|	 1,500 	|		|		|	https://smartstore.naver.com/0109/products/2233911416
18	|	O	|	Electronics	|	Arduino Uno	|	1	|	-	|	 - 	|		|		|	
19	|	O	|	Electronics	|	CNC Shield	|	1	|	 18,000 	|	 18,000 	|	CNC Shield + A4988 Driver x 4 + CH340G(Arduino Uno Compatible)	|	미스터조각기	|	https://smartstore.naver.com/mrcnc/products/760201081
20	|	O	|	Electronics	|	12V 2A Wall Transformer	|	1	|	$10.99 	|	 12,436 	|		|	amazon	|	https://www.amazon.com/Adapter-100-240V-Transformers-Switching-Adaptor/dp/B019Q3U72M
21	|	O	|	Electronics	|	2-4 limit switches	|	-	|		|		|	optional. I suggest you leave them off and add later if you want them	|		|	
22	|	O	|	H/W	|	624zz bearings with the idler pulley	|	-	|		|		|		|		|	https://www.thingiverse.com/thing:2424284	
23	|	O	|	H/W	|	M8 와셔	|	4	|	70	|	280	|		|	영원툴	|	https://smartstore.naver.com/0109/products/2262082335	
24	|	O	|	H/W	|	M8 육각너트 스텐 서스	|	4	|	40	|	160	|		|	영원툴	|	https://smartstore.naver.com/0109/products/2233911416	
25	|	O	|	H/W	|	CG0 서보모터 연장케이블	|	1	|	2,660	|	2,660	|		|		|	http://item.gmarket.co.kr/detailview/item.asp?goodscode=923930300

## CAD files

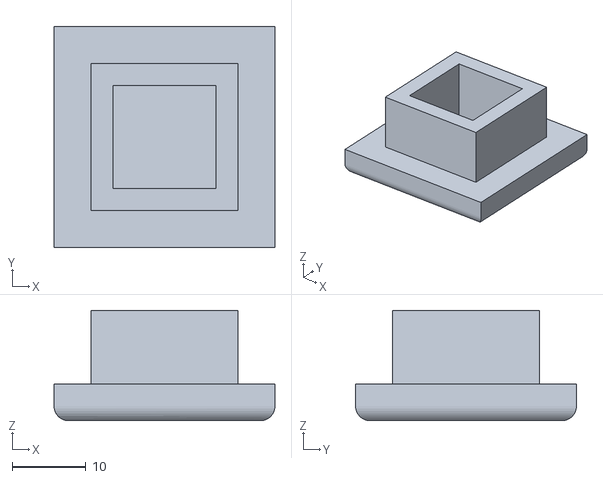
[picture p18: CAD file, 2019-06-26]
3D_Printer/cap_tester.stl
30.0 x 30.0 x 15.0

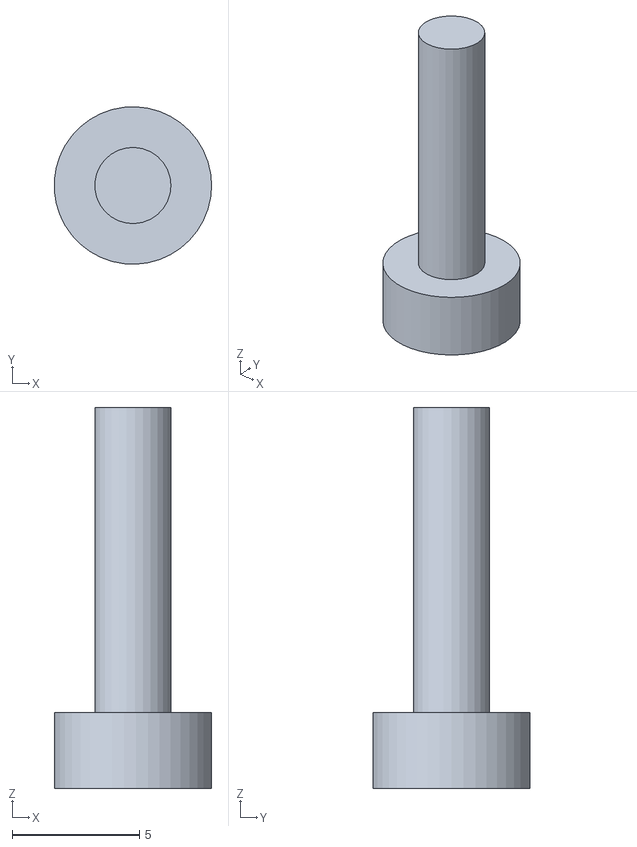
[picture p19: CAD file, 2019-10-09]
drawingTool/models/spring-holder.stl
6.19 x 6.20 x 15.0

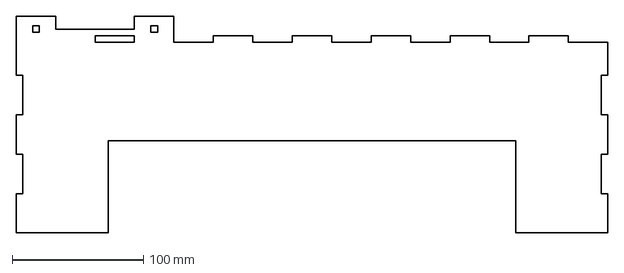
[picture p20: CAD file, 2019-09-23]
drawingTool/models/plate_side-20190923_2p.dxf
450.0 x 165.0 mm

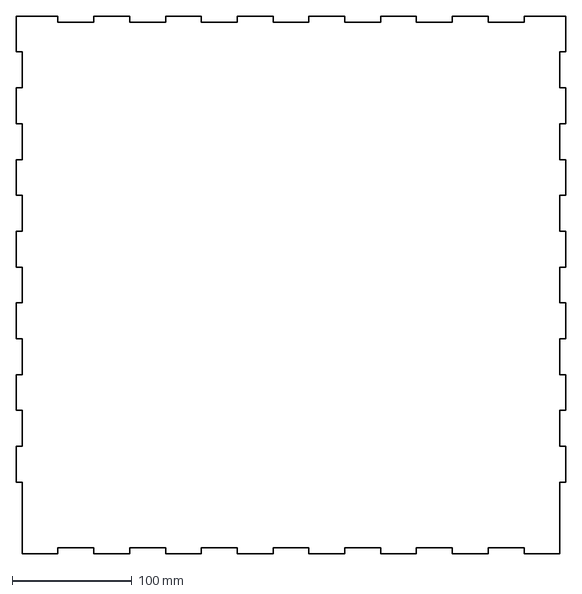
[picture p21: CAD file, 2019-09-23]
drawingTool/models/plate_top-20190923_1p.dxf
460.0 x 450.0 mm

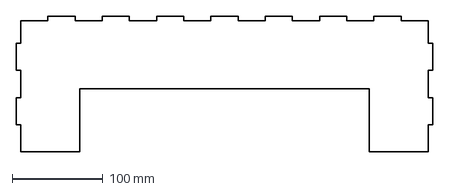
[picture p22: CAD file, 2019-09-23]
drawingTool/models/plate_front_back-20190923_2p.dxf
460.0 x 150.0 mm

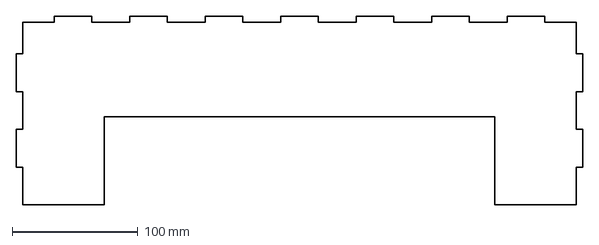
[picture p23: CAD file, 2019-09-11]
drawingTool/models/plate_front-20190911.dxf
450.0 x 150.0 mm

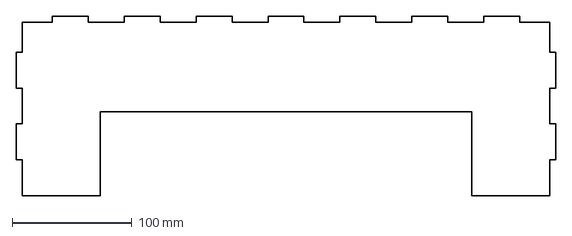
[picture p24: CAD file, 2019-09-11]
drawingTool/models/plate_back-20190911.dxf
450.0 x 150.0 mm

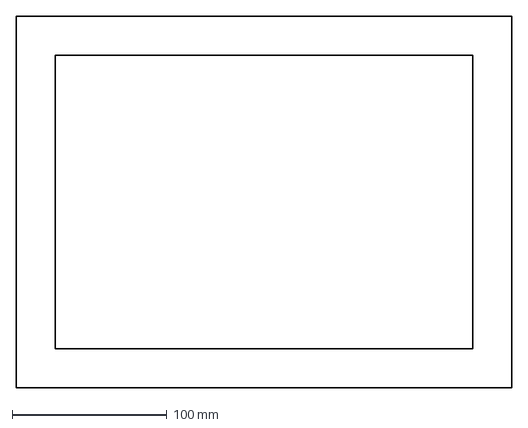
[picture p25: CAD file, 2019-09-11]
drawingTool/models/drawing guide.dxf
320.0 x 240.0 mm

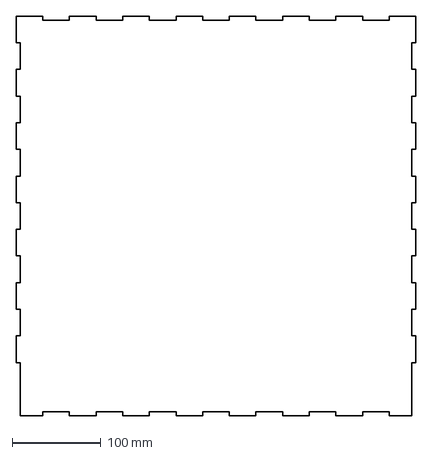
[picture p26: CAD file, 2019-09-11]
drawingTool/models/plate_top-20190911.dxf
450.0 x 450.0 mm

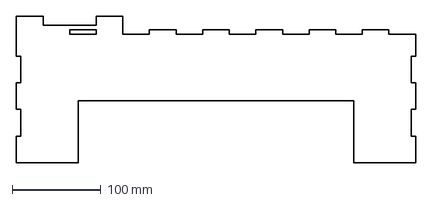
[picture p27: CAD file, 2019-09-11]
drawingTool/models/plate_right-20190911.dxf
450.0 x 165.0 mm

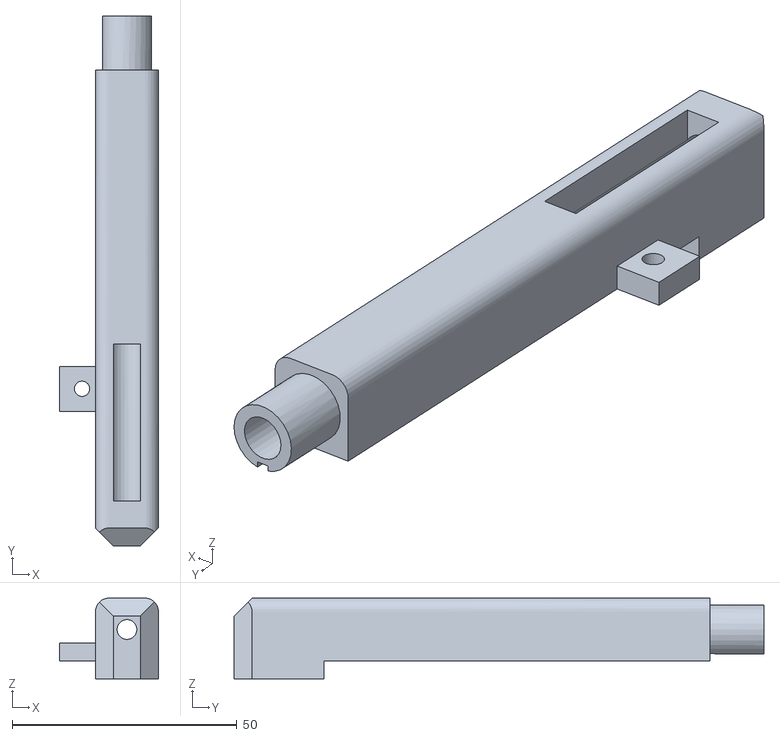
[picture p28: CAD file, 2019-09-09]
drawingTool/models/new_penholder_with_window.stl
22.0 x 118.0 x 18.0

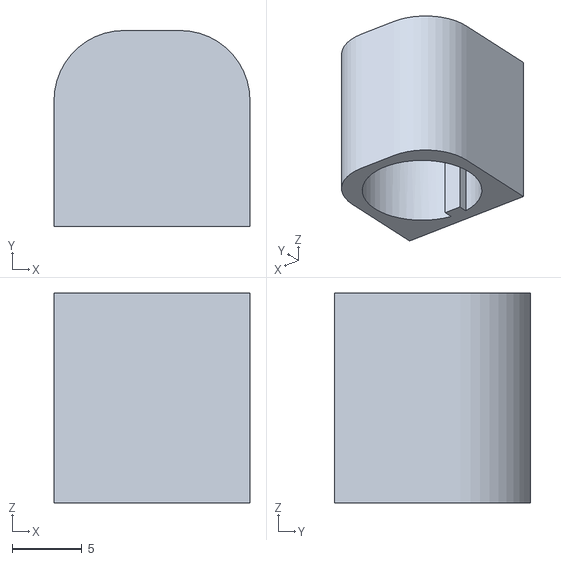
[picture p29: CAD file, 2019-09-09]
drawingTool/models/new_penholdercap.stl
14.0 x 14.0 x 15.0

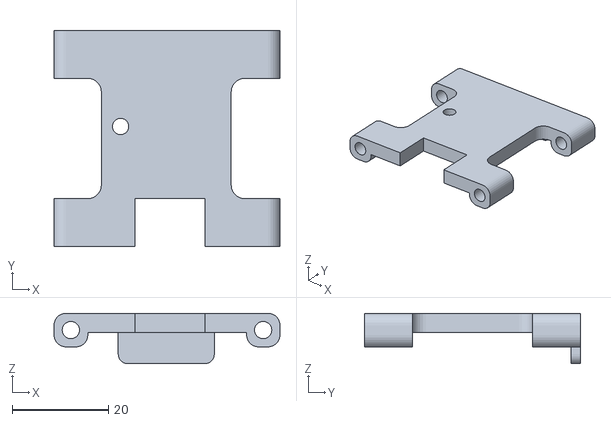
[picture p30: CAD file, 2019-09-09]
drawingTool/models/new_slider.stl
47.0 x 45.0 x 10.5

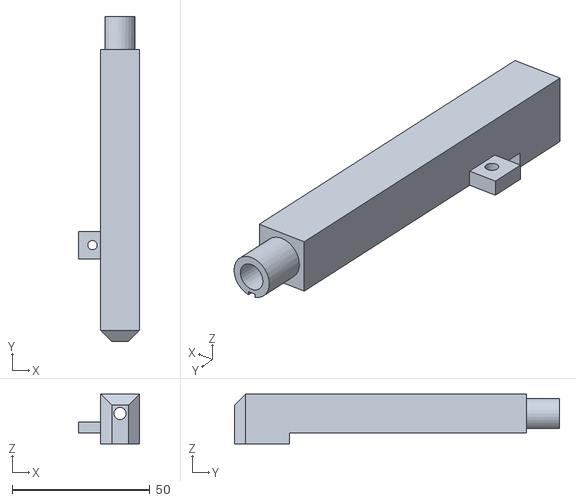
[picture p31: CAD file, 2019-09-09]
drawingTool/models/new_penholder.stl
22.0 x 118.0 x 18.0

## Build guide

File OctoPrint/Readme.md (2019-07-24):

# 1. Prerequites
 - <a href="https://octopi.octoprint.org/latest">OctoPrint Download</a><br>
 - <a href="https://github.com/pbatard/rufus/releases/download/v3.5/rufus-3.5p.exe">rufs portable Download(@Windows)</a><br>
  . <a href="https://m.blog.naver.com/PostView.nhn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">How to make a OctoPrint image on SD card, using rufs tool</a>
# 2. Installation
  ### Your Raspberry Pi(@OctoPrint)
  - ID : **pi**, Password : **raspberry**<br>
  - $cd boot > $nano pctopi-wpa-supplicant.txt<br>
  - ...<br>
    network={<br>
      ssid=**"YOUR_AP_NAME"**<br>
      psk=**"YOUR_AP_PW"**<br>
    }<br>
    ...<br>
  - ^X > Y<br>
  - $ifconfig > Checking the IP address of your OctoPrint device: (e.g.)192.168.0.x<br>
  - $sudo raspi-config > Choice "5. Interfacing Options" > Choice "P2 SSH" > Choice "Yes"<br>
  - $passwd pi > Changement the password of your OctoPrint device<br>
  - $sudo reboot
  ### Your PC(@Ubuntu)
  - $sudo apt-get install putty<br>
  - $putty > Host Name: "YOUR_OCTOPRINT_DEVICE_IP" > Saved Sessions: "OctoPrint" > Click the "Save" button > Click the "Open" button
# 3. Making case for devices of OctoPrint
 - <a href="https://www.thingiverse.com/thing:2797774/remixes">CR-10 RaspberryPi Ethernet Camera Mount Kit</a><br>
 - Feature 1<br>
   
# 4. Port Fowarding
 - Naver > Searching with the keyword like "ip주소확인" > Checking your private IP used at home<br>
 - ipTIME > 192.168.0.1 > Log-in > Advanced Setup > NAT/Routing > Port Forwarding > + Add new rule > Input "Rule Name" > Choice "Port Foward(User) > Input "Internal IP" such like 192.168.0.x > Choice "TCP" on the field of Protocol > Input "XXXX" on the left filed of External port > Input "XX" on the left field of Internal port > Click the "Modify" button 
# 5. Blogs
 - <a href="https://cosmosjs.blog.me/221516473588">라즈베리파이와 OctoPrint를 이용한 3D 프린터 원격제어</a>
 - <a href="https://seoulworkshop.blog.me/221265052717">공유기 포트포워딩 설정하기</a>
 - <a href="https://m.blog.naver.com/PostView.nhn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">OctoPrint 세팅 2 - OctoPi 설치 및 WiFi 연결 설정</a>
 - <a href="https://studyforus.tistory.com/27">외부IP에서 내 컴퓨터(내부 IP)로 접속하기</a>
 - <a href="https://bugwhale.com/raspberry-octoprint-install-02/">라즈베리파이에 옥토프린트 설치하기 - 02. 초기 설정하기</a>
 - <a href="https://bugwhale.com/raspberry-octoprint-install-04/">라즈베리파이에 옥토프린트 설치하기 - 04. 전원 작업하기</a>

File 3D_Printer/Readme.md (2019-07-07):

# Cura Print settings
   ## Prerequites
   - Cura 4.1.0
   - CR-10S5 or ANET A8(Prusa i3)
   - OctoPrint 1.3.11
   ## Settings
   ```
   This setting is based on my experience.
   If you have nice recommendations better than me, please let me know.
   For reference, if necessary, I will update continuously.
   ```
   ### Quality
   - Layer Height : 0.2mm
   - initial Layer Height : 0.26mm
   - Line Width : 0.4mm
       - Wall Line Width : 0.4mm
           - Outer Wall Line Width : 0.4mm
           - Inner Wall(s) Line Width : 0.4mm
       - Top/Bottom Line Width : 0.4mm
       - Infill Line Width : 0.4mm
       - Initial Layer Line Width : 100%
   ### Shell
   - Wall Thickness : 0.8mm
       - Wall Line Count : 2
   - Top/Bottom Thickness : 0.8mm
       - Top Thickness : 0.8mm
           - Top Layers : 4
       - Bottom Thickness : 0.8mm
           - Bottom Layers : 4
   - Top/Bottom Pattern : Concentric
       ```
       Lines, zig zag, concentric and 'line direction' with custom value [90]
       ```
       
   - Optimize Wall Printing Order : check
   - Fill Gaps Between Walls : Everywhere
       <br>
   - Horizontal Expansion : 0mm
   - Enable Ironing : check
   ### Infill
   - Infill Density : 15%
       - Infill Line Distance : 8.0mm
   - Infill Pattern : <a href="https://ultimaker.com/en/resources/52670-infill">Cubic Subdivision</a>
     ```
     Grid: Strong 2D infill
     Lines: Quick 2D infill
     Triangles: Strong 2D infill
     Tri-hexagon: Strong 2D infill
     Cubic: Strong 3D infill
     Cubic (subdivision): Strong 3D infill (this saves material compared to Cubic)
     Octet: Strong 3D infill
     Quarter cubic: Strong 3D infill
     Concentric: Flexible 3D infill
     Concentric 3D : Flexible 3D infill
     Zig-zag: A grid shaped infill, printing continuously in one diagonal direction
     Cross: Flexible 3D infill
     Cross 3D: Flexible 3D infill
     ```
     
   - Infill Line Multiplier : 1
   - Infill Overlap Percentage : 10%<br>
       <br>
   - Infill Layer Thickness : 0.2mm
   - Infill Before Walls : no check
   ### Material
   - Printing Temperature : 185℃
   - Printing Temperature Initial Layer : 185℃
   - Initial Printing Temperature : 175℃
   - Final Printing Temperature : 170℃
   - Build Plate Temperature : 20℃
   - Build Plate Temperature Initial Layer : 20℃
   - Enable Retraction : check
   - Retract at Layer Change : check
   - Retraction Distance : 10
   - Retraction Speed : 100mm/s
   ### Speed
   - Print Speed : 50mm/s
       - Infill Speed : 30mm/s
       - Wall Speed : 25.0mm/s
           - Outer Wall Speed : 30mm/s
           - Inner Wall Speed : 50mm/s
       - Top/Bottom Speed : 20m/s
       - Support Speed : 40mm/s
           - Support Infill Speed : 50mm/s
           - Support Interface Speed : 26.6667mm/s
               - Support Floor Speed : 30mm/s
   - Travel Speed : 100mm/s
   - Initial Layer Speed : 25.0mm/s
       - Initial Layer Print Speed : 20mm/s
       - Initial Layer Travel Speed : 30mm/s
   - Skirt/Brim Speed : 30mm/s
   - Maximum Z Speed : 100mm/s
   - Enable Acceleration Control : no check
   - Enable Jerk Control : no check
   ### Travel
   - Combining Mode : Off
   - Avoid Printed Parts When Traveling : check
   - Z Hop When Retracted : check
   - Z Hop Only Over Printed Parts : no check
   - Z Hop Height : 0.5mm
   ### Cooling
   - Enable Print Cooling : check
   - Fan Speed : 100.0%
      - Regular Fan Speed : 100.0%
      - Maximum Fan Speed : 100.0%
   - Regular/Maximum Speed Threshold : 10s
   - Initial Fan Speed : 0%
   - Regular Fan Speed at Height : 0.32mm
       - Regular Fan Speed at Layer : 2
   - Minimum Layer Time : 0
   - Minimum Speed : 10mm/s
   - Lift Head : no check
   ### Support
   - Generate Support : check
   - Support Placement : Everywhere
   - Support Overhang Angle : 50
   - Support Pattern : <a href="https://ultimaker.com/en/resources/20422-cura-support-settings">Triangles</a>
     
   - Support Density : 15%
   - Support Horizontal Expansion : 0mm
   - Support Infil Layer Thickness : 0.2mm
   - Gradual Support Infill Steps : 0
   - Enable Support Interface : check
       - Enable Support Roof : check
       - Enable Support Floor : check
   ### Build Plate Adhesion
   - Build Plate Adhesion Type : Brim
   - Brim Width : 6mm
       - Brim Line Count : 15
   - Brim Only on Outside : no check
   ### Dual Extrusion : No item
   ### Special Modes
   - Print Sequence : All at Once
   - Surface Mode : Normal
   - Spiralize Outer Contour : no check
   ### Experimental : No item

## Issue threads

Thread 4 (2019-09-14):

[ERR] core dumped in function 'pyrDown'

electop, 2019-09-14:
cv2.error: OpenCV(4.1.1) ../modules/imgproc/src/pyramids.cpp:729: error: (-215:Assertion failed) !_src.empty() in function 'pyrDown_' Aborted (core dumped)

electop, 2019-09-14:
In this case, user should make the directory of './images' on the execution path.

Closed 2019-09-14.

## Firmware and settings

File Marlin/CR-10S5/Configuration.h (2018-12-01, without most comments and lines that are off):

#define CONFIGURATION_H
#include "boards.h"
#include "macros.h"
#if ENABLED(USE_AUTOMATIC_VERSIONING)
  #include "_Version.h"
#else
  #include "Default_Version.h"
#endif
#define STRING_CONFIG_H_AUTHOR "(CR-10S 500)" // Who made the changes.
#define SHOW_BOOTSCREEN
#define STRING_SPLASH_LINE1 SHORT_BUILD_VERSION // will be shown during bootup in line 1
#define SERIAL_PORT 0
#define BAUDRATE 115200
  #define MOTHERBOARD BOARD_RAMPS_13_EFB
#define CUSTOM_MACHINE_NAME "Marlin 1.9.1 Ready"
#define EXTRUDERS 1
#define POWER_SUPPLY 1
#define TEMP_SENSOR_0 1
#define TEMP_SENSOR_1 0
#define TEMP_SENSOR_2 0
#define TEMP_SENSOR_3 0
#define TEMP_SENSOR_BED 1
#define MAX_REDUNDANT_TEMP_SENSOR_DIFF 10
#define TEMP_RESIDENCY_TIME 10  // (seconds)
#define TEMP_HYSTERESIS 3       // (degC) range of +/- temperatures considered "close" to the target one
#define TEMP_WINDOW     1       // (degC) Window around target to start the residency timer x degC early.
#define HEATER_0_MINTEMP 5
#define HEATER_1_MINTEMP 5
#define HEATER_2_MINTEMP 5
#define HEATER_3_MINTEMP 5
#define BED_MINTEMP 5
#define HEATER_0_MAXTEMP 275
#define HEATER_1_MAXTEMP 275
#define HEATER_2_MAXTEMP 275
#define HEATER_3_MAXTEMP 275
#define BED_MAXTEMP 150
#define PIDTEMP
#define BANG_MAX 255 // limits current to nozzle while in bang-bang mode; 255=full current
#define PID_MAX BANG_MAX // limits current to nozzle while PID is active (see PID_FUNCTIONAL_RANGE below); 255=full current
  #define PID_FUNCTIONAL_RANGE 10 // If the temperature difference between the target temperature and the actual temperature
  #define PID_INTEGRAL_DRIVE_MAX PID_MAX  //limit for the integral term
  #define K1 0.95 //smoothing factor within the PID
  #define  DEFAULT_Kp 22.2
  #define  DEFAULT_Ki 1.08
  #define  DEFAULT_Kd 114
#define MAX_BED_POWER 255 // limits duty cycle to bed; 255=full current
#define PREVENT_DANGEROUS_EXTRUDE
#define PREVENT_LENGTHY_EXTRUDE
#define EXTRUDE_MINTEMP 170
#define EXTRUDE_MAXLENGTH (X_MAX_LENGTH+Y_MAX_LENGTH) //prevent extrusion of very large distances.
#define THERMAL_PROTECTION_HOTENDS // Enable thermal protection for all extruders
#define THERMAL_PROTECTION_BED     // Enable thermal protection for the heated bed
#define ENDSTOPPULLUPS // Comment this out (using // at the start of the line) to disable the endstop pullup resistors
const bool X_MIN_ENDSTOP_INVERTING = false; // set to true to invert the logic of the endstop.
const bool Y_MIN_ENDSTOP_INVERTING = false; // set to true to invert the logic of the endstop.
const bool Z_MIN_ENDSTOP_INVERTING = false; // set to true to invert the logic of the endstop.
const bool X_MAX_ENDSTOP_INVERTING = true; // set to true to invert the logic of the endstop.
const bool Y_MAX_ENDSTOP_INVERTING = true; // set to true to invert the logic of the endstop.
const bool Z_MAX_ENDSTOP_INVERTING = true; // set to true to invert the logic of the endstop.
const bool Z_MIN_PROBE_ENDSTOP_INVERTING = true; // set to true to invert the logic of the endstop.
#define X_ENABLE_ON 0
#define Y_ENABLE_ON 0
#define Z_ENABLE_ON 0
#define E_ENABLE_ON 0 // For all extruders
#define DISABLE_X false
#define DISABLE_Y false
#define DISABLE_Z false
#define DISABLE_E false // For all extruders
#define DISABLE_INACTIVE_EXTRUDER true //disable only inactive extruders and keep active extruder enabled
#define INVERT_X_DIR false
#define INVERT_Y_DIR false
#define INVERT_Z_DIR true
#define INVERT_E0_DIR false
#define INVERT_E1_DIR false
#define INVERT_E2_DIR false
#define INVERT_E3_DIR false
#define X_HOME_DIR -1
#define Y_HOME_DIR -1
#define Z_HOME_DIR -1
#define min_software_endstops false // If true, axis won't move to coordinates less than HOME_POS.
#define max_software_endstops true  // If true, axis won't move to coordinates greater than the defined lengths below.
#define X_MIN_POS 0
#define Y_MIN_POS 0
#define Z_MIN_POS 0
#define X_MAX_POS 510
#define Y_MAX_POS 510
#define Z_MAX_POS 510
#define FILAMENT_RUNOUT_SENSOR // Uncomment for defining a filament runout sensor such as a mechanical or opto endstop to check the existence of filament
  const bool FIL_RUNOUT_INVERTING = true;  // Should be uncommented and true or false should assigned
  #define ENDSTOPPULLUP_FIL_RUNOUT // Uncomment to use internal pullup for filament runout pins if the sensor is defined.
  #define FILAMENT_RUNOUT_SCRIPT "M600"
#define AUTO_BED_LEVELING_FEATURE // Delete the comment to enable (remove // at the start of the line)
#define Z_MIN_PROBE_REPEATABILITY_TEST  // If not commented out, Z-Probe Repeatability test will be included if Auto Bed Leveling is Enabled.
  #define AUTO_BED_LEVELING_GRID
    #define LEFT_PROBE_BED_POSITION 45
    #define RIGHT_PROBE_BED_POSITION 455
    #define FRONT_PROBE_BED_POSITION 45
    #define BACK_PROBE_BED_POSITION 455
    #define MIN_PROBE_EDGE 10 // The Z probe minimum square sides can be no smaller than this.
    #define AUTO_BED_LEVELING_GRID_POINTS 5
  #define X_PROBE_OFFSET_FROM_EXTRUDER 0     // Z probe to nozzle X offset: -left  +right
  #define Y_PROBE_OFFSET_FROM_EXTRUDER 0     // Z probe to nozzle Y offset: -front +behind
  #define Z_PROBE_OFFSET_FROM_EXTRUDER -0.2  // Z probe to nozzle Z offset: -below (always!)
  #define Z_RAISE_BEFORE_HOMING 8       // (in mm) Raise Z axis before homing (G28) for Z probe clearance.
  #define XY_TRAVEL_SPEED 3000         // X and Y axis travel speed between probes, in mm/min.
  #define Z_RAISE_BEFORE_PROBING 15   // How much the Z axis will be raised before traveling to the first probing point.
  #define Z_RAISE_BETWEEN_PROBINGS 5  // How much the Z axis will be raised when traveling from between next probing points.
  #define Z_RAISE_AFTER_PROBING 15    // How much the Z axis will be raised after the last probing point.
  #define Z_SAFE_HOMING   // This feature is meant to avoid Z homing with Z probe outside the bed area.
    #define Z_SAFE_HOMING_X_POINT ((X_MIN_POS + X_MAX_POS) / 2)    // X point for Z homing when homing all axis (G28).
    #define Z_SAFE_HOMING_Y_POINT ((Y_MIN_POS + Y_MAX_POS) / 2)    // Y point for Z homing when homing all axis (G28).
#define HOMING_FEEDRATE {50*60, 50*60, 4*60, 0}  // set the homing speeds (mm/min)
#define DEFAULT_AXIS_STEPS_PER_UNIT   {80.00,80.00,400.00,93.0}  // default steps per unit for Ultimaker
#define DEFAULT_MAX_FEEDRATE          {300, 300, 5, 25}    // (mm/sec)
#define DEFAULT_MAX_ACCELERATION      {300, 300, 100,5000}    // X, Y, Z, E maximum start speed for accelerated moves. E default values are good for skeinforge 40+, for older versions raise them a lot.
#define DEFAULT_ACCELERATION          500    // X, Y, Z and E max acceleration in mm/s^2 for printing moves
#define DEFAULT_RETRACT_ACCELERATION  500   // X, Y, Z and E max acceleration in mm/s^2 for retracts
#define DEFAULT_TRAVEL_ACCELERATION 1000    // X, Y, Z acceleration in mm/s^2 for travel (non printing) moves
#define DEFAULT_XYJERK                5.0    // (mm/sec)
#define DEFAULT_ZJERK                 0.4     // (mm/sec)
#define DEFAULT_EJERK                 5.0    // (mm/sec)
#define CUSTOM_M_CODES
    #define CUSTOM_M_CODE_SET_Z_PROBE_OFFSET 851
    #define Z_PROBE_OFFSET_RANGE_MIN -20
    #define Z_PROBE_OFFSET_RANGE_MAX 20
#define EEPROM_SETTINGS
  #define EEPROM_CHITCHAT // Please keep turned on if you can.
#define PLA_PREHEAT_HOTEND_TEMP 185
#define PLA_PREHEAT_HPB_TEMP 0
#define PLA_PREHEAT_FAN_SPEED 0   // Insert Value between 0 and 255
#define ABS_PREHEAT_HOTEND_TEMP 240
#define ABS_PREHEAT_HPB_TEMP 0
#define ABS_PREHEAT_FAN_SPEED 0   // Insert Value between 0 and 255
#define LANGUAGE_INCLUDE_CN GENERATE_LANGUAGE_INCLUDE(cn)
#define LANGUAGE_INCLUDE_KANA GENERATE_LANGUAGE_INCLUDE(kana)
  #define DISPLAY_CHARSET_HD44780_JAPAN        // this is the most common hardware
#define SDSUPPORT // Enable SD Card Support in Hardware Console
#define POWEROFF_SAVE_SD_FILE // If power off, after power on, the printing can be resumed.
#define Z_TO_HOME           // IF auto bed level enabled, it need to enabled.
#define REPRAP_DISCOUNT_FULL_GRAPHIC_SMART_CONTROLLER
#define SOFT_PWM_SCALE 0
#define FILAMENT_SENSOR_EXTRUDER_NUM 0   //The number of the extruder that has the filament sensor (0,1,2)
#define MEASUREMENT_DELAY_CM        14   //measurement delay in cm.  This is the distance from filament sensor to middle of barrel
#define DEFAULT_NOMINAL_FILAMENT_DIA 1.75  //Enter the diameter (in mm) of the filament generally used (3.0 mm or 1.75 mm) - this is then used in the slicer software.  Used for sensor reading validation
#define MEASURED_UPPER_LIMIT         3.30  //upper limit factor used for sensor reading validation in mm
#define MEASURED_LOWER_LIMIT         1.90  //lower limit factor for sensor reading validation in mm
#define MAX_MEASUREMENT_DELAY       20     //delay buffer size in bytes (1 byte = 1cm)- limits maximum measurement delay allowable (must be larger than MEASUREMENT_DELAY_CM  and lower number saves RAM)
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

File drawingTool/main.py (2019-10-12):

import sys
from PyQt5.QtCore import *
from PyQt5.QtGui import *
from PyQt5.QtWidgets import *
import cv2
import numpy as np
import datetime
import serial
import time

#global variable for file name (does not work)
strFilename1 = "./images/screen_capture_cartoonized_mask_.jpg"
strFilename2 = "./images/screen_capture_cartoonized_.jpg"
 
QApplication.setAttribute(Qt.AA_EnableHighDpiScaling, True)

# gcode sender function
# open serial port and write each gcode (and get return)
# need to install phtyon pySerial
def simpleGcodesender():
    s = serial.Serial("/dev/ttyUSB1",115200)
    #/dev/ttyUSB0
    print("Opening Serial Port")
    f = open("faceGcode.gcode","r")
    # Wake up 
    s.write(str.encode("\r\n\r\n")) # Hit enter a few times to wake the Printrbot
    time.sleep(2)   # Wait for Printrbot to initialize
    s.flushInput()  # Flush startup text in serial input
    print("Sending gcode")

    for line in f:
        l = removeComment(line)
        l = l.strip() # Strip all EOL characters for streaming
        if (l.isspace()==False and len(l)>0):
            #print("Sending: " + l)
            #s.write(l + "\n") # Send g-code block
            s.write(str.encode(l + "\n"))
            grbl_out = s.readline() # Wait for response with carriage return
            #print(" : " + grbl_out.strip())
 
    # Wait here until printing is finished to close serial port and file.
    #raw_input("  Press <Enter> to exit.")
    # Close file and serial port
    f.close()
    s.close()
    print("Drawing is over")

    


#gcode comment remover
#Eliminate gocde comment
def removeComment(string):
    if (string.find(';')==-1):
        return string
    else:
        return string[:string.index(';')]



# import capture function
# Function for Camera Ready
def cam(now):
    cap = cv2.VideoCapture(0)

    while(True):
        # Capture frame-by-frame
        ret, frame = cap.read()

        # Our operations on the frame come here
        gray = cv2.cvtColor(frame, cv2.COLOR_BGR2GRAY)

        # Display the resulting frame
        cv2.imshow('frame',gray)
        if cv2.waitKey(1) & 0xFF == ord('q'):
            cv2.imwrite("./images/screen_capture_%s.jpg" % now, frame)
            break

    # When everything done, release the capture
    cap.release()
    cv2.destroyAllWindows()

# Function for cartoonizing
# based on image processing
# make it as 1 color drawing
# save jpg file in the ./images/ folder
def cartoonizer(now):
    num_down = 2       # number of downsampling steps
    num_bilateral = 7  # number of bilateral filtering steps
    
    img_rgb = cv2.imread("./images/screen_capture_%s.jpg" % now)
 
    # downsample image using Gaussian pyramid
    img_color = img_rgb
    for _ in range(num_down):
        img_color = cv2.pyrDown(img_color)
    
    # repeatedly apply small bilateral filter instead of
    # applying one large filter
    for _ in range(num_bilateral):
        img_color = cv2.bilateralFilter(img_color, d=9,
                                        sigmaColor=9,
                                        sigmaSpace=7)
    
    # upsample image to original size
    for _ in range(num_down):
        img_color = cv2.pyrUp(img_color)

    # convert to grayscale and apply median blur
    img_gray = cv2.cvtColor(img_rgb, cv2.COLOR_RGB2GRAY)
    img_blur = cv2.medianBlur(img_gray, 7)
    rows, cols, channels = img_rgb.shape
    roi = img_color[0:rows, 0:cols]

    # detect and enhance edges
    img_edge = cv2.adaptiveThreshold(img_blur, 255,
                                    cv2.ADAPTIVE_THRESH_MEAN_C,
                                    cv2.THRESH_BINARY,
                                    blockSize=9,
                                    C=2)

    img_median = cv2.medianBlur(img_edge, 5)
    edge_compare = np.concatenate((img_edge, img_median), axis=1)
    cv2.imshow("edge_compare", edge_compare)
    ret, mask = cv2.threshold(img_median, 10, 255, cv2.THRESH_BINARY)
    mask_inv = cv2.bitwise_not(mask)

    # convert back to color, bit-AND with color image
    img_edge = cv2.cvtColor(img_median, cv2.COLOR_GRAY2RGB)
    #img_cartoon = cv2.bitwise_and(img_color, img_edge)

    img_cartoon_bg = cv2.bitwise_and(roi, roi, mask = mask)
    img_cartoon_fg = cv2.bitwise_and(img_edge, img_edge, mask = mask_inv)
    dst = cv2.add(img_cartoon_fg, img_cartoon_bg)
    img_color[0:rows, 0:cols] = dst

    # display
    #cv2.imshow("original", img_rgb)
    #cv2.imshow("edge", img_edge)
    #cv2.imshow("mask_inv", mask_inv)
    #cv2.imshow("color", img_color)
    #cv2.imshow("mask", mask)
    #cv2.imshow("cartoon", img_rgb)
    result_compare = np.concatenate((img_rgb, img_color), axis=1)
    cv2.imshow("result_compare", result_compare)
    cv2.waitKey(0)

    strFilename1 = "./images/screen_capture_cartoonized_mask_" + now + ".jpg"
    strFilename2 = "./images/screen_capture_cartoonized_" + now + ".jpg"

    #cv2.imwrite("./images/screen_capture_cartoonized_mask_%s.jpg" % now, mask)
    #cv2.imwrite("./images/screen_capture_cartoonized_%s.jpg" % now, img_rgb)
    cv2.imwrite("a.jpg", mask)
    cv2.imwrite(strFilename2, img_rgb)
    cv2.destroyAllWindows()


def imageCapturenCartoonizer():
    now = str(datetime.datetime.now())[:-7]
    cam(now)
    cartoonizer(now)

# Modify pixcel point to real mili meter point
# make it actual length for X and Y
def convertPixelX2mm(i):
    return i * 210 / 680

def convertPixelY2mm(i):
    return i * 148 / 480

# Modify drawing bot coordinate point
# absolute coordinate is - Y area
def convertRealY(y):
    return 0-y

# UI design using QWidget
#
class CWidget(QWidget): 
 
    def __init__(self):
 
        super().__init__()
 
        # 전체 폼 박스
        formbox = QHBoxLayout()
        self.setLayout(formbox)
 
        # 좌, 우 레이아웃박스
        left = QVBoxLayout()
        right = QVBoxLayout()
 
        # 그룹박스1 생성 및 좌 레이아웃 배치
        gb = QGroupBox('그리기 종류')        
        left.addWidget(gb)
 
        # 그룹박스1 에서 사용할 레이아웃
        box = QVBoxLayout()
        gb.setLayout(box)        
 
        # 그룹박스 1 의 라디오 버튼 배치
        text = ['line', 'Curve', 'Rectange', 'Ellipse']
        self.radiobtns = []
 
        for i in range(len(text)):
            self.radiobtns.append(QRadioButton(text[i], self))
            self.radiobtns[i].clicked.connect(self.radioClicked)
            box.addWidget(self.radiobtns[i])
 
        self.radiobtns[0].setChecked(True)
        self.drawType = 0
         
        # 그룹박스2
        gb = QGroupBox('펜 설정')        
        left.addWidget(gb)        
 
        grid = QGridLayout()      
        gb.setLayout(grid)        
 
        label = QLabel('선굵기')
        grid.addWidget(label, 0, 0)
 
        self.combo = QComboBox()
        grid.addWidget(self.combo, 0, 1)       
 
        for i in range(1, 21):
            self.combo.addItem(str(i))
 
        label = QLabel('선색상')
        grid.addWidget(label, 1,0)        
         
        self.pencolor = QColor(0,0,0)
        self.penbtn = QPushButton()        
        self.penbtn.setStyleSheet('background-color: rgb(0,0,0)')
        self.penbtn.clicked.connect(self.showColorDlg)
        grid.addWidget(self.penbtn,1, 1)

        # 그룹박스3
        gb = QGroupBox('붓 설정')        
        left.addWidget(gb)
 
        hbox = QHBoxLayout()
        gb.setLayout(hbox)
 
        label = QLabel('붓색상')
        hbox.addWidget(label)                
 
        self.brushcolor = QColor(255,255,255)
        self.brushbtn = QPushButton()        
        self.brushbtn.setStyleSheet('background-color: rgb(255,255,255)')
        self.brushbtn.clicked.connect(self.showColorDlg)
        hbox.addWidget(self.brushbtn)
 
        # 그룹박스4
        gb = QGroupBox('지우개')        
        left.addWidget(gb)
 
        hbox = QHBoxLayout()
        gb.setLayout(hbox)        
         
        self.checkbox  =QCheckBox('지우개 동작')
        self.checkbox.stateChanged.connect(self.checkClicked)
        hbox.addWidget(self.checkbox)
 
        # 그룹박스5
        gb = QGroupBox('CAPTURE')        
        left.addWidget(gb)

        hbox = QHBoxLayout()
        gb.setLayout(hbox)
 
        self.capturebtn = QPushButton()
        self.capturebtn.setIcon(QIcon(QPixmap("cam.png")))        
        #self.capturebtn.setStyleSheet('background-color: rgb(255,255,255)')
        self.capturebtn.clicked.connect(self.captureImageDlg)
        hbox.addWidget(self.capturebtn)
       
        # 그룹박스6
        gb = QGroupBox('DRAW')        
        left.addWidget(gb)

        hbox = QHBoxLayout()
        gb.setLayout(hbox)
 
        self.drawbtn = QPushButton()
        self.drawbtn.setIcon(QIcon(QPixmap("pen.png")))        
        self.drawbtn.clicked.connect(self.drawStartDlg)
        hbox.addWidget(self.drawbtn)

        left.addStretch(1)        
          
        # 우 레이아웃 박스에 그래픽 뷰 추가
        self.view = CView(self)       
        right.addWidget(self.view)        
 
        # 전체 폼박스에 좌우 박스 배치
        formbox.addLayout(left)
        formbox.addLayout(right)
 
        formbox.setStretchFactor(left, 0)
        formbox.setStretchFactor(right, 1)
         
        self.setGeometry(100, 100, 800, 500) 
         
    def radioClicked(self):
        for i in range(len(self.radiobtns)):
            if self.radiobtns[i].isChecked():
                self.drawType = i                
                break
 
    def checkClicked(self):
        pass



    def captureImageDlg(self):
    
        imageCapturenCartoonizer()

        # Capture image as a.jpg and reload on the right view              
        pic = QPixmap("a.jpg") 
        self.view.scene.addItem(QGraphicsPixmapItem(pic))  

        pass

    # no need dialogbox but start to drawing
    def drawStartDlg(self):
        str="M05 S10\nG01 F10000\nG01 X0 Y0"
        self.view.f.write(str)
        self.view.f.close()
        print("file closed")
        simpleGcodesender()
        pass
             
    def showColorDlg(self):       
         
        # 색상 대화상자 생성      
        color = QColorDialog.getColor()
 
        sender = self.sender()
 
        # 색상이 유효한 값이면 참, QFrame에 색 적용
        if sender == self.penbtn and color.isValid():           
            self.pencolor = color
            self.penbtn.setStyleSheet('background-color: {}'.format( color.name()))
        else:
            self.brushcolor = color
            self.brushbtn.setStyleSheet('background-color: {}'.format( color.name()))
 
        
# QGraphicsView display QGraphicsScene
#
class CView(QGraphicsView):
    
    def __init__(self, parent):
 
        super().__init__(parent)       
        self.scene = QGraphicsScene()
        self.scene.setSceneRect(0, 0, 2400, 1200) 
        pic = QPixmap("s.jpg") 
        self.scene.addItem(QGraphicsPixmapItem(pic))  

        self.setScene(self.scene)
 
        self.items = []
         
        self.start = QPointF()
        self.end = QPointF()
 
        self.setRenderHint(QPainter.HighQualityAntialiasing)

        # Start Writing GCode        
        self.f = open("faceGcode.gcode","w")
        self.f.write("G10 P0 L20 X0 Y0 Z0\n")
        self.f.write("M03 S030\n")
        self.f.write("M05 S10\n")
        self.f.write("G90\n")
        self.f.write("G21\n")

 
    def moveEvent(self, e):
        rect = QRectF(self.rect())
        rect.adjust(0,0,-2,-2)
 
        self.scene.setSceneRect(rect)

  
 
    def mousePressEvent(self, e):
 
        if e.button() == Qt.LeftButton:
            # 시작점 저장
            self.start = e.pos()
            self.end = e.pos()
            str="G01 F10000\nG01 X%4.3f Y%4.3f\nM03 S60\nG01 F1000\n" %(convertPixelX2mm(self.start.x()), convertRealY(convertPixelY2mm(self.start.y())))
            self.f.write(str)
 
    def mouseMoveEvent(self, e):  
         
        # e.buttons()는 정수형 값을 리턴, e.button()은 move시 Qt.Nobutton 리턴 
        if e.buttons() & Qt.LeftButton:           
 
            self.end = e.pos()

 
            if self.parent().checkbox.isChecked():
                pen = QPen(QColor(255,255,255), 10)
                path = QPainterPath()
                path.moveTo(self.start)
                path.lineTo(self.end)
                self.scene.addPath(path, pen)
                self.start = e.pos()
                return None
 
            pen = QPen(self.parent().pencolor, self.parent().combo.currentIndex())
 
            # 직선 그리기
            if self.parent().drawType == 0:
                 
                # 장면에 그려진 이전 선을 제거            
                if len(self.items) > 0:
                    self.scene.removeItem(self.items[-1])
                    del(self.items[-1])                
 
                # 현재 선 추가
                line = QLineF(self.start.x(), self.start.y(), self.end.x(), self.end.y())                
                self.items.append(self.scene.addLine(line, pen))
 
            # 곡선 그리기
            if self.parent().drawType == 1:
 
                
                str="G01 X%4.3f Y%4.3f\n" %(convertPixelX2mm(self.end.x()), convertRealY(convertPixelY2mm(self.end.y())))
                self.f.write(str)
                #print(str) 
                # Path 이용
                path = QPainterPath()
                path.moveTo(self.start)
                path.lineTo(self.end)
                self.scene.addPath(path, pen)
 
                # Line 이용
                #line = QLineF(self.start.x(), self.start.y(), self.end.x(), self.end.y())
                #self.scene.addLine(line, pen)
                 
                # 시작점을 다시 기존 끝점으로
                self.start = e.pos()
 
            # 사각형 그리기
            if self.parent().drawType == 2:
                brush = QBrush(self.parent().brushcolor)
 
                if len(self.items) > 0:
                    self.scene.removeItem(self.items[-1])
                    del(self.items[-1])
 
 
                rect = QRectF(self.start, self.end)
                self.items.append(self.scene.addRect(rect, pen, brush))
                 
            # 원 그리기
            if self.parent().drawType == 3:
                brush = QBrush(self.parent().brushcolor)
 
                if len(self.items) > 0:
                    self.scene.removeItem(self.items[-1])
                    del(self.items[-1])
 
 
                rect = QRectF(self.start, self.end)
                self.items.append(self.scene.addEllipse(rect, pen, brush))
 
 
    def mouseReleaseEvent(self, e):        
 
        if e.button() == Qt.LeftButton:
 
            if self.parent().checkbox.isChecked():
                return None
 
            pen = QPen(self.parent().pencolor, self.parent().combo.currentIndex())
 
            if self.parent().drawType == 0:
 
                self.items.clear()
                line = QLineF(self.start.x(), self.start.y(), self.end.x(), self.end.y())
                 
                self.scene.addLine(line, pen)

                # Add end point of line
                str="G01 X%4.3f Y%4.3f\n" %(convertPixelX2mm(self.end.x()), convertRealY(convertPixelY2mm(self.end.y())))
                self.f.write(str)
 
            if self.parent().drawType == 2:
 
                brush = QBrush(self.parent().brushcolor)
 
                self.items.clear()
                rect = QRectF(self.start, self.end)
                self.scene.addRect(rect, pen, brush)

                # Add Rectangle piont 
                str="G01 X%4.3f Y%4.3f\n" %(convertPixelX2mm(self.end.x()), convertRealY(convertPixelY2mm(self.start.y())))
                self.f.write(str)
                str="G01 X%4.3f Y%4.3f\n" %(convertPixelX2mm(self.end.x()), convertRealY(convertPixelY2mm(self.end.y())))
                self.f.write(str)
                str="G01 X%4.3f Y%4.3f\n" %(convertPixelX2mm(self.start.x()), convertRealY(convertPixelY2mm(self.end.y())))
                self.f.write(str)
                str="G01 X%4.3f Y%4.3f\n" %(convertPixelX2mm(self.start.x()), convertRealY(convertPixelY2mm(self.start.y())))
                self.f.write(str)
 
 
            if self.parent().drawType == 3:
 
                brush = QBrush(self.parent().brushcolor)
 
                self.items.clear()
                rect = QRectF(self.start, self.end)
                self.scene.addEllipse(rect, pen, brush)


                str="M05 S10\nG01 F10000\nG01 X%4.3f Y%4.3f\nM03 S60\n" %(convertPixelX2mm(self.start.x()), convertRealY(convertPixelY2mm(self.start.y() + (self.end.y() - self.start.y())/2 )))
                self.f.write(str)
                
                #print("start x %d y %d\n" %(self.start.x(), self.start.y()))
                #print("start x %d y %d\n" %(self.end.x(), self.end.y()))

                #print("G02 X%4.3f Y%4.3f\n" %(convertPixelX2mm(self.start.x()),convertRealY(convertPixelY2mm(self.start.y()))
                #print("G02 X%4.3f Y%4.3f\n" %(convertPixelX2mm(self.end.x()), convertRealY(convertPixelY2mm(self.end.y())))

                # Add circle piont 
                str="G02 F1000 X%4.3f Y%4.3f I%4.3f\n" %(convertPixelX2mm(self.start.x()), convertRealY(convertPixelY2mm(self.start.y() + (self.end.y() - self.start.y())/2)), convertPixelX2mm((self.end.x()-self.start.x())/2))
                self.f.write(str)

        # When sending g code to drawing bot file is already closed. So this command cause error
        # need to flag when drawing bot is operated
        self.f.write("M05 S10\n")
 
 
if __name__ == '__main__':
    app = QApplication(sys.argv)
    w = CWidget()
    w.show()
    sys.exit(app.exec_())

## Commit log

2019-05-17 Update Drawing Robot.md
    구매 내역 반영
2019-07-09 error gcode sample
2019-09-09 drawing bot penholder CAD(STL) files
    SARASA PEN Holder
    - holder
    - slide
    - spring cap
    - cap
    [new_penholder.stl, new_penholder_with_window.stl, new_penholdercap.stl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]
2019-09-11 maker faire drawing bot desk
    메이커 페어에서 사용할 로봇 테이블입니다.
    상판, 좌우(대칭), 앞 뒤, 종이 홀더로 구성되어 있습니다
    [drawing guide.dxf, plate_back-20190911.dxf, plate_front-20190911.dxf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]
2019-09-11 desk image
    메이커 페어 데스크 레이저 커팅용 이미지 파일입니다
2019-09-23 450 x 450 TABLE
    가로 방향 내면이 450이 되도록 수정하였습니다.
    윗면 1장, 앞뒤 좌우는 동일 형상으로 1개의 데이터로 2장 만들면 됩니다. (1p는 1장, 2P는 2장 제작)
    [plate_front_back-20190923_2p.dxf, plate_side-20190923_2p.dxf, plate_top-20190923_1p.dxf]
2019-10-09 spring holder
    You can use sarasa pen sping with this holder.
    [spring-holder.stl]
2019-10-12 modify Gcode creation
    It has bug when start to draw just pen down. So First drawing with pen down status.
    I add pen down and pen up once more so it can solved.
    [main.py]
2019-10-12 Drawing speed for circle
    is too slow. Speed up for 1000 (current 300)
    [main.py]
2019-10-12 배경 GCODE
    미완성인데 일단 올립니다 경복궁 외관 동그라미, Maker Faire 글씨 정도가들어가 있어요
